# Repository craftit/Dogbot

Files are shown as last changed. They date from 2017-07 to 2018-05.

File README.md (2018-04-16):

# Dogbot

[DogBot] is a quadruped robot developed by [React AI] as a platform for researching robotics, AI and more.

The Dogbot repository contains CAD designs, along with software for higher-level systems for control and operation of the [React AI] DogBot robot via [ROS].  It utilises the lower-level motor control firmware in the corresponding [Firmware] repository for interaction with the physical DogBot.

# Installation

This code has been tested for installation and operation on Ubuntu Linux.

[ROS] must be installed; the code has been tested against the Kinetic release.  The repository contains a [catkin](http://wiki.ros.org/catkin) workspace under [Software/ROS](./Software/ROS), which should be built with `catkin build`

You may need to install the packages `ros-kinetic-rosparam-shortcuts ros-kinetic-ros-control ros-kinetic-ros-controllers` 

# Operation via Firmware and ROS

## Home the motors

The motors must be ‘homed’, i.e. know their absolute position, before they can be controlled via the ROS driver, hence they must first be controlled via the UI as described in the [Firmware] repo.

**Note:** complete the Firmware UI steps before starting the ROS components.  The hardware interface node in ROS will send conflicting signals if it is operational while the UI tries to alter the motor positions.

## Quick Start

To get started with ROS control, build and source the code then run `dogbot_hardware.launch`

```bat
cd Software/ROS
catkin build
source devel/setup.bash
roslaunch dogbot_control dogbot_hardware.launch
```

This launches a hardware interface node of type dogbot_control/dogbot_hw_main, which uses the [ros_control](http://wiki.ros.org/controller_manager) package to spawn and interact with ROS controllers.  This provides a framework for different controller types, as well as standardising interactions with Gazebo and RViz.

If you are controlling other equipment you may require a different launch file, such as testrig_hardware.launch

## Further ROS Control

The motors can now be controlled by interacting directly with ROS topics or via ROS nodes. Further details are in the ROS directory [readme file](./Software/ROS)

# Contributing

If you have any problems with the contents of either repository, or have a question about [DogBot], please feel free to [contact us](https://www.reactai.com/)

If you wish to contribute please fork the project on GitHub.  More details on contributing to follow.

# License

details to follow

[DogBot]: https://www.reactai.com/dog-bot/
[React AI]: https://www.reactai.com
[ROS]: http://www.ros.org
[Firmware]: https://github.com/craftit/BMC2-Firmware

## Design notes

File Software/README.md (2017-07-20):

Currently the motor controller firmware can be found in another repository.

  https://github.com/craftit/BMC2-Firmware

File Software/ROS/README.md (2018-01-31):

# Dogbot ROS Components

DogBot is integrated with ROS for ease of integration with your own systems.  Refer to the main [Dogbot repo] instructions for initial setup.

# Operation

## Initial Operation and Controllers

Interaction with the hardware requires the firmware components found in the [Firmware] repo, and the motors reqiure 'homing' via the firmware UI.  Once this is done, basic components can be run up using:

```bat
cd Software/ROS
catkin build
source devel/setup.bash
roslaunch dogbot_control dogbot_hardware.launch
```

12 controllers are instantiated, e.g. *front_right_knee_joint_controller*.  The [ros_control](http://wiki.ros.org/controller_manager) package is used to spawn and interact with ROS controllers, with the outline code beign built around Dave Coleman's [boilerplate] examples.

Currently the hardware interface only operates for position controllers, and only accepts absolute positions, not relative ones (hence the motors must be homed).

## Control via Topics, examples

Show the current joint states: ```rostopic echo -n 1 /dogbot/joint_states```

Sample output:
```
header: 
  seq: 307571
  stamp: 
    secs: 1517397784
    nsecs: 684705073
  frame_id: ''
name: [front_right_roll_joint, front_right_pitch_joint, front_right_knee_joint, front_left_roll_joint,
  front_left_pitch_joint, front_left_knee_joint, back_right_roll_joint, back_right_pitch_joint,
  back_right_knee_joint, back_left_roll_joint, back_left_pitch_joint, back_left_knee_joint]
position: [0.10201127827167511, 0.09683401137590408, 0.8471538424491882, 0.05003453932963618, -0.0013422536430880427, -0.010162778198719025, 0.00364325987175107, -0.002109255874529481, -0.012463783845305443, 0.006903018802404404, 0.013039035722613335, 0.0074782706797122955]
velocity: [0.0, 0.0, 0.0, 0.0, 0.0, 0.0, 0.0, 0.0, 0.0, 0.0, 0.0, 0.0]
acceleration: [0.0, 0.0, 0.0, 0.0, 0.0, 0.0, 0.0, 0.0, 0.0, 0.0, 0.0, 0.0]
```

Show just front_right_knee_joint position: ```rostopic echo -n 1 /dogbot/joint_states/position[2]```

Set a joint position:
```rostopic pub /dogbot/front_right_knee_position_controller/command std_msgs/Float64 "data: -1.0" -1```

[boilerplate]: https://github.com/davetcoleman/ros_control_boilerplate
[Dogbot repo]: https://github.com/craftit/Dogbot
[ROS]: http://www.ros.org
[Firmware]: https://github.com/craftit/BMC2-Firmware

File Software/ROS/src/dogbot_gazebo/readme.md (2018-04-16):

# dogbot_gazebo

Controls operation of simulated DogBot(s) in gazebo.  The robot description is in the dogbot_description package.

Control software is in dogbot_control, as the same software drives the simulation and the hardware

# Quick start

<pre>
cd Software/ROS
catkin build
source devel/setup.bash
roslaunch dogbot_gazebo gztest.launch
</pre>

Then to send commands to the joints and make the simulated DogBot move its legs around, in roughly a walking-on-the-spot motion, switch to another window and type:

<pre>
cd src/dogbot_gazebo/bags/
rosbag play -l demo1.bag
</pre>

# Launch files

Top-level files start with gz

Other files are components, intended to be included into the higher-level files (esp. to set the namespace correctly)

# Prerequisites

Ensure you have gazebo-ros control packages installed, http://wiki.ros.org/gazebo_ros_control

<pre>sudo apt-get install ros-kinetic-gazebo-ros-pkgs ros-kinetic-gazebo-ros-control</pre>

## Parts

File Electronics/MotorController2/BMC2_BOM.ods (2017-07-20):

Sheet: BMC2
Reference | Value | Footprint | Datasheet | Done
U1 | TJA1042T/3 | Housings_SOIC:SOIC-8_3.9x4.9mm_Pitch1.27mm |  | x
P2 | CAN
C1 | 0.1uf (6V min) | Capacitors_SMD:C_0805_HandSoldering |  | x
P4 | USB_OTG
R9 | 22R | Resistors_SMD:R_0805_HandSoldering |  | x
R10 | 22R | Resistors_SMD:R_0805_HandSoldering |  | x
D1 | 10V | Diodes_SMD:DO-214AB_Handsoldering |  | x
R1 | 1k | Resistors_SMD:R_0805_HandSoldering |  | x
R2 | 1k | Resistors_SMD:R_0805_HandSoldering |  | x
R3 | 1k | Resistors_SMD:R_0805_HandSoldering |  | x
R4 | 1k | Resistors_SMD:R_0805_HandSoldering |  | x
R5 | 1k | Resistors_SMD:R_0805_HandSoldering |  | x
R8 | 1k | Resistors_SMD:R_0805_HandSoldering |  | x
R7 | 10k | Resistors_SMD:R_0805_HandSoldering |  | x
C2 | 0.1uF | Capacitors_SMD:C_0805_HandSoldering |  | x
R6 | 1k | Resistors_SMD:R_0805_HandSoldering |  | x
P3 | DATA
P5 | PhaseA
P6 | PhaseB
P7 | PhaseC
W1 | TEST_1P
W2 | TEST_1P
P1 | Sensor
P9 | VSUPPLY
P10 | GND
X1 | 8MHz
C5 | 15pF | Capacitors_SMD:C_0805_HandSoldering |  | x
C6 | 15pF | Capacitors_SMD:C_0805_HandSoldering |  | x
P8 | CONN_02X05
C13 | 100nf | Capacitors_SMD:C_0805_HandSoldering |  | x
C10 | 100nf | Capacitors_SMD:C_0805_HandSoldering |  | x
C12 | 100nf | Capacitors_SMD:C_0805_HandSoldering |  | x
C11 | 100nf | Capacitors_SMD:C_0805_HandSoldering |  | x
C9 | 100nf 5V | Capacitors_SMD:C_0805_HandSoldering |  | x
C8 | 4.7uf | Capacitors_SMD:C_1206_HandSoldering |  | x
C14 | 1uf | Capacitors_SMD:C_0805_HandSoldering |  | x
R13 | 10R | Resistors_SMD:R_0805_HandSoldering |  | x
L1 | INDUCTOR | Resistors_SMD:R_0805_HandSoldering
C7 | 100nf | Capacitors_SMD:C_0805_HandSoldering |  | x
SW1 | RESET
JP2 | Jumper_NC_Small | Resistors_SMD:R_0805_HandSoldering |  | x
JP1 | Jumper_NO_Small | Resistors_SMD:R_0805_HandSoldering |  | x
C4 | 2.2uf | Capacitors_SMD:C_0805_HandSoldering |  | x
C3 | 2.2uf | Capacitors_SMD:C_0805_HandSoldering |  | x
U2 | STM32F205RBTx | LQFP64
R11 | 100R | Resistors_SMD:R_0805_HandSoldering |  | x
D2 | GREEN LED | LEDs:LED_0805
R12 | 100R | Resistors_SMD:R_0805_HandSoldering |  | x
D3 | RED LED | LEDs:LED_0805
R16 | 10K | Resistors_SMD:R_0805_HandSoldering |  | x
R17 | 10K | Resistors_SMD:R_0805_HandSoldering |  | x
C16 | 0.1uF 5V | Capacitors_SMD:C_0805_HandSoldering |  | x
R15 | 10K | Resistors_SMD:R_0805_HandSoldering |  | x
SW2 | CAL
R14 | 10K | Resistors_SMD:R_0805_HandSoldering |  | x
C15 | 0.1uF 5V | Capacitors_SMD:C_0805_HandSoldering |  | x
W14 | TEST_1P
U3 | DRV8305 |  |  | x
R19 | 10K | Resistors_SMD:R_0805_HandSoldering |  | x
R18 | 10K | Resistors_SMD:R_0805_HandSoldering |  | x
C23 | 0.047uf 45v | Capacitors_SMD:C_1206_HandSoldering |  | x
C22 | 0.047uf 90V | Capacitors_SMD:C_1206_HandSoldering |  | x
C20 | 1uf 6.3V | Capacitors_SMD:C_0805_HandSoldering |  | x
C19 | 1uf 6.3V | Capacitors_SMD:C_0805_HandSoldering |  | x
C18 | 1uf 16V | Capacitors_SMD:C_1206_HandSoldering |  | x
C27 | 2.2uf 16V | Capacitors_SMD:C_1206_HandSoldering |  | x
C28 | 4.7uF 45V | Capacitors_SMD:C_1206_HandSoldering |  | x
R22 | 100R | Resistors_SMD:R_0805_HandSoldering |  | x
R26 | R001
R25 | R001
R24 | R001
Q3 | BSC016N06NS
Q4 | BSC016N06NS
Q6 | BSC016N06NS
Q5 | BSC016N06NS
Q1 | BSC016N06NS
Q2 | BSC016N06NS
R29 | 39K | Resistors_SMD:R_0805_HandSoldering |  | x
R30 | 3K | Resistors_SMD:R_0805_HandSoldering |  | x
R31 | 39K | Resistors_SMD:R_0805_HandSoldering |  | x
R32 | 3K | Resistors_SMD:R_0805_HandSoldering |  | x
C35 | 30pF 5V | Capacitors_SMD:C_0805_HandSoldering |  | x
C34 | 30pF 5V | Capacitors_SMD:C_0805_HandSoldering |  | x
R27 | 39K | Resistors_SMD:R_0805_HandSoldering |  | x
R28 | 3K | Resistors_SMD:R_0805_HandSoldering |  | x
C33 | 30pF 5V | Capacitors_SMD:C_0805_HandSoldering |  | x
C30 | 0.1uf 50V min | Capacitors_SMD:C_1206_HandSoldering |  | x
C31 | 0.1uf (Min 50V) | Capacitors_SMD:C_1206_HandSoldering |  | x
C32 | 0.1uf (Min 50V) | Capacitors_SMD:C_1206_HandSoldering |  | x
R20 | 39K | Resistors_SMD:R_0805_HandSoldering |  | x
R21 | 3K | Resistors_SMD:R_0805_HandSoldering |  | x
C21 | 0.1uF 5V | Capacitors_SMD:C_0805_HandSoldering |  | x
C17 | 1uF 4V | Capacitors_SMD:C_0805_HandSoldering |  | x
C24 | 1nF 5V | Capacitors_SMD:C_0805_HandSoldering |  | x
C26 | 1nF 5V | Capacitors_SMD:C_0805_HandSoldering |  | x
C29 | 1nf 5V | Capacitors_SMD:C_0805_HandSoldering |  | x
W5 | TEST_1P
W4 | TEST_1P
W3 | TEST_1P
W7 | GHA
W8 | GLA
W9 | SLA
W6 | SHA
C25 | 0.1uF 5V | Capacitors_SMD:C_0805_HandSoldering |  | x
R23 | 10K | Resistors_SMD:R_0805_HandSoldering |  | x
TH1 | THERMISTOR
C38 | 22nF 6V | Capacitors_SMD:C_0805_HandSoldering |  | x
R33 | 22k | Resistors_SMD:R_0805_HandSoldering |  | x
D4 | D | Diodes_SMD:DO-214AB_Handsoldering |  | x
C36 | 220nF 60V | Capacitors_SMD:C_1206_HandSoldering |  | x
L2 | 47uH | Inductors:SELF-WE-PD3S
C39 | 220nF 60V | Capacitors_SMD:C_1206_HandSoldering |  | x
C37 | 100uF 60V | Capacitors_SMD:c_elec_10x10.5 |  | x
C40 | 220nF 6V | Capacitors_SMD:C_0805_HandSoldering |  | x
D6 | 50V | Diodes_SMD:SOD-123 |  | x
C41 | 100uF 6V | Capacitors_SMD:c_elec_6.3x5.8 |  | x
C42 | 220nF 6V | Capacitors_SMD:C_0805_HandSoldering |  | x
L3 | 47uH | Inductors:SELF-WE-PD3S
D7 | 5.6V | Diodes_SMD:SOD-123 |  | x
D9 | LED | LEDs:LED_0805
R34 | 100R | Resistors_SMD:R_0805_HandSoldering |  | x
U4 | IFX91041EJV50
D5 | D | Diodes_SMD:DO-214AB_Handsoldering |  | x
C43 | 1uF 4V min | Capacitors_SMD:C_0805_HandSoldering |  | x
D8 | 3.6V | Diodes_SMD:SOD-123 |  | x
U5 | TC2117-3.3V |  |  | x
W12 | 5V
W13 | 3V3
W10 | DSUP
W11 | GND

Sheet: Sheet2
Boards | 12
Part | Footprint | Per Board | Total | Farnell code
1K | R 0805 | 7 | 84 | 2447587
10K | R 0805 | 8 | 96 | 9332391
22R | R 0805 | 2 | 24 | 2447609
100R | R 0805 | 4 | 48 | 9333703
39K | R 0805 | 4 | 48 | 2447646
3K | R 0805 | 4 | 48 | 2447648
22K | R 0805 | 1 | 12 | 2447607
0.1uF 50V | C 0805 | 13 | 156 | 1759265
0.1uF 250V | C 1206 | 3 | 36 | 1828957
15pf | C 0805 | 2 | 24 | 2497014
4.7uF 25V | C 1206 | 1 | 12 | 1828835
4.7uF 100V | C 1206 | 1 | 12 | 2310265
1uf 50V | C 0805 | 6 | 72 | 1759432
1uF 100V | C 1206 | 4 | 48 | 2320876
2.2uF 50V | C 0805 | 2 | 24 | 2611933
2.2uF 50V | C 1206 | 1 | 12 | 1797017
30pf | C 0805 | 3 | 36 | 2581093
47nf 200V | C 1206 | 2 | 24 | 1855874
0R | R 0805 | 2 | 24 | 2309111
1nF 50V | C 0805 | 6 | 72 | 9406344
22nF | C 0805 | 1 | 12 | 2320841
220nf 100V | C 1206 | 2 | 24 | 1856615
100uf 63V | c_elec_10x10.5 | 1 | 12 | 9696040
220nf | C 0805 | 2 | 24 | 1759173
100uf | c_elec_6.3x5.8 | 1 | 12 | 2611349
Schottky 60V | SOD-123 | 4 | 48 | 2284958
TC2117-3.3V |  | 1 | 12 | 1605581
Zener 3.6V | SOD-123 | 1 | 12 | 1651592
Zener 5.6V | SOD-123 | 1 | 12 | 1431292
Thermistor | R 0805 | 2 | 24 | 2103179
LED Green | LED 0805 | 1 | 12 | 1465996
LED Red | LED 0805 | 1 | 12 | 1581239
LED Yellow | LED 0805 | 1 | 12 | 1581241
10uH | L 0805 | 1 | 12 | 2215650
9 Way Right Angle |  | 1 | 12 | 2468365
4 way Right Angle |  | 2 | 24 | 588738
5 way right angle |  | 1 | 12 | 588740
push button |  | 2 | 24 | 2468741
10R | R 0805 | 1 | 12 | 2447556

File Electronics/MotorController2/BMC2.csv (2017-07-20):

Reference, Quantity, Value, Footprint, Datasheet, Order, Farnell, Farnell Related, Plug Farnell, Notes, Note, Order2, Part, Type
C1 C10 C11 C12 C13 C15 C16 C2 C21 C25 C44 C7 C9 ,13,"0.1uF 50V","Capacitors_SMD:C_0805_HandSoldering","","","","","","",",","1759265",",",",",",","
C14 C17 C19 C20 C43 ,5,"1uF 50V","Capacitors_SMD:C_0805_HandSoldering","","","","","","",",","1759432",",","5V",",",","
C18 C30 C31 C32 ,4,"1uF 100V","Capacitors_SMD:C_1206_HandSoldering","","","","","","",",","2320876",",","16V",",",","
C22 C23 ,2,"47nF 200V","Capacitors_SMD:C_1206_HandSoldering","","","","","","",",","1855874",",","45V",",",","
C27 ,1,"2.2uF 50V","Capacitors_SMD:C_1206_HandSoldering","","","","","","",",","1797017",",","16V",",",","
C28 ,1,"4.7uF 100V","Capacitors_SMD:C_1206_HandSoldering","","","","","","",",","1797017",",","45V",",",","
C33 C34 C35 ,3,"30pF 5V","Capacitors_SMD:C_0805_HandSoldering","","","","","","",",","2581093",",",",",",","
C36 C39 ,2,"220nF 100V","Capacitors_SMD:C_1206_HandSoldering","","","","","","",",","1856615",",",",",",","
C37 ,1,"100uF 63V","Capacitors_SMD:c_elec_10x10.5","","","","","","",",","9696040",",",",",",","
C38 ,1,"22nF 50V","Capacitors_SMD:C_0805_HandSoldering","","","","","","",",","2581093",",","6V",",",","
C3 C4 ,2,"2.2uF 50V","Capacitors_SMD:C_0805_HandSoldering","","","","","","",",","2611933",",",",",",","
C40 C42 ,2,"220nF 100V","Capacitors_SMD:C_0805_HandSoldering","","","","","","",",","1856615",",","6V",",",","
C41 ,1,"100uF 6.3V","Capacitors_SMD:c_elec_6.3x5.8","","","","","","",",","2611349",",",",",",","
C24 C26 C29 C45 C46 C47 ,6,"1nF 50V","Capacitors_SMD:C_0805_HandSoldering","","","","","","",",","9406344",",",",",",","
C5 C6 ,2,"15pF","Capacitors_SMD:C_0805_HandSoldering","","","","","","",",","2497014",",",",",",","
C8 ,1,"4.7uF 25V","Capacitors_SMD:C_1206_HandSoldering","","","","","","",",","1828835",",",",",",","
D1 D4 D5 D6 ,4,"60V 2A","Diodes_SMD:SOD-123","","","","","","",",","2284958",",",",",",","
D2 ,1,"GREEN LED","LEDs:LED_0805","","","","","","",",","1465996",",","2V",",",","
D3 ,1,"YELLOW","LEDs:LED_0805","","","","","","",",","1581241",",",",",",","
D7 ,1,"5.6V","Diodes_SMD:SOD-123","","","","","","",","http://uk.farnell.com/on-semiconductor/mmsz5v6t1g/diode-zener-5-6v-0-5w/dp/1431292","1431292",",",",",","MMSZ5V6T1G","
D8 ,1,"3.6V","Diodes_SMD:SOD-123","","","","","","",","http://uk.farnell.com/on-semiconductor/mmsz4685t1g/diode-zener-vz-3-6v/dp/1651592","1651592",",",",",","MMSZ4685T1G","
D9 ,1,"RED","LEDs:LED_0805","","","","","","",",","1581239",",",",",",","
JP1 ,1,"Jumper_NO_Small","Resistors_SMD:R_0805_HandSoldering","","","","","","","
JP2 ,1,"Jumper_NC_Small","Resistors_SMD:R_0805_HandSoldering","","","","","","","
L1 ,1,"10uH","Resistors_SMD:R_0805_HandSoldering","","","","","","",",","2215650",",",",",",","
L2 L3 ,2,"47uH","Inductors:SELF-WE-PD3S","","","","","","",","http://uk.farnell.com/tdk/clf7045t-470m/inductor-47uh-1-3a-20-smd/dp/2345091",",",",",",",","
P1 ,1,"Sensor","Pin_Headers:Pin_Header_Angled_1x09","","","","","","",",","2468365",","1098695",",",",","
P10 ,1,"GND","Connect:1pin","","","","","","","
P11 ,1,"I2C","Pin_Headers:Pin_Header_Straight_1x04","","","","","","",","http://uk.farnell.com/molex/171856-0004/connector-header-tht-2-54mm-4way/dp/2366182",",",",",",",","
P12 P2 ,2,"CAN","Pin_Headers:Pin_Header_Angled_1x04","","","","","","",",","588738","1098455",",",",",","
P3 ,1,"DATA","Pin_Headers:Pin_Header_Angled_1x05","","","","","","",",","588740",",",",",",","
P4 ,1,"USB_OTG","Connect:USB_Mini-B","","","","","","",","http://uk.farnell.com/molex/67503-1020/mini-usb-2-0-otg-type-b-rcpt-smt/dp/1125348",",",",",",",","
P5 ,1,"PhaseA","Connect:1pin","","","","","","","
P6 ,1,"PhaseB","Connect:1pin","","","","","","","
P7 ,1,"PhaseC","Connect:1pin","","","","","","","
P8 ,1,"CONN_02X05","Local:SMT-HDR-10","","","","","","",","http://uk.rs-online.com/web/p/pcb-headers/0451732/?searchTerm=FTSH-105-01-F-DV-K&autocorrected=y",",",",",",",","
P9 ,1,"VSUPPLY","Connect:1pin","","","","","","","
Q1 Q2 Q3 Q4 Q5 Q6 ,6,"BSC016N06NS","Local:SON127P532X615X110-8N","","","","","","","
R1 R2 R3 R4 R5 R6 R8 ,7,"1k","Resistors_SMD:R_0805_HandSoldering","","","","","","",","http://uk.farnell.com/multicomp/mcwr08x1001ftl/res-thick-film-1k-1-0-125w-0805/dp/2447587",",",",",",",","
R11 R12 R22 R34 ,4,"100R","Resistors_SMD:R_0805_HandSoldering","","","","","","","
R13 ,1,"10","Resistors_SMD:R_0805_HandSoldering","","","","","","","
R24 R25 R26 ,3,"R001","Local:R_PSR400_SENSE","","","","","","","
R20 R27 R29 R31 ,4,"39K","Resistors_SMD:R_0805_HandSoldering","","","","","","","
R21 R28 R30 R32 ,4,"3K","Resistors_SMD:R_0805_HandSoldering","","","","","","","
R33 ,1,"22k","Resistors_SMD:R_0805_HandSoldering","","","","","","","
R14 R15 R16 R17 R18 R19 R23 R7 ,8,"10K","Resistors_SMD:R_0805_HandSoldering","","","","","","","
R10 R9 ,2,"22R","Resistors_SMD:R_0805_HandSoldering","","","","","","","
SW1 ,1,"RESET","Buttons_Switches_SMD:SW_SPST_FSMSM","","","","","","",",","42468741",",",",",",","
SW2 ,1,"CAL","Buttons_Switches_SMD:SW_SPST_FSMSM","","","","","","",","http://uk.farnell.com/alcoswitch-te-connectivity/1437566-3/pushbutton-switch-spst-0-05a-24v/dp/2468741","2468741",",",",",",","
TH1 ,1,"NTC 10K","Resistors_SMD:R_0805_HandSoldering","","","","","","",","http://uk.farnell.com/vishay/ntcs0805e3103jlt/thermistor-10k-5-smd-ntc/dp/2103179","2103179",",",",",",","
U1 ,1,"TJA1042T/3","Housings_SOIC:SOIC-8_3.9x4.9mm_Pitch1.27mm","","","","","","",","http://uk.farnell.com/nxp/tja1042t-3-1j/can-transceiver-aec-q100-2mbps/dp/2574957",",",",",",",","
U2 ,1,"STM32F205RBTx","Housings_QFP:LQFP-64_10x10mm_Pitch0.5mm","","","","","","","
U3 ,1,"DRV8305","QFP50P900X900X120-49N:QFP50P900X900X120-49N","","","","","","","
U4 ,1,"IFX91041EJV50","Housings_SOIC:SOIC-8-1EP_3.9x4.9mm_Pitch1.27mm","","","","","","",","https://www.digikey.co.uk/product-detail/en/infineon-technologies/IFX91041EJ-V50/IFX91041EJ-V50INCT-ND/3300395",",",",",",",","
U5 ,1,"TC2117-3.3V","TO_SOT_Packages_SMD:SOT-223","","","","","","",","http://uk.farnell.com/microchip/tc2117-3-3vdbtr/ic-cmso-ldo-3-3v-800ma-sot223/dp/1605581",",",",",",",","
W1 ,1,"CAN_TX","Measurement_Points:Measurement_Point_Round-SMD-Pad_Small","","","","","","","
W10 ,1,"DSUP","Measurement_Points:Measurement_Point_Round-SMD-Pad_Small","","","","","","","
W11 ,1,"GND","Measurement_Points:Measurement_Point_Round-SMD-Pad_Big","","","","","","","
W12 ,1,"5V","Measurement_Points:Measurement_Point_Round-SMD-Pad_Small","","","","","","","
W13 ,1,"3V3","Measurement_Points:Measurement_Point_Round-SMD-Pad_Small","","","","","","","
W14 ,1,"PB12","Measurement_Points:Measurement_Point_Round-SMD-Pad_Small","","","","","","","
W2 ,1,"CAN_RX","Measurement_Points:Measurement_Point_Round-SMD-Pad_Small","","","","","","","
W3 ,1,"ISenseA","Measurement_Points:Measurement_Point_Round-SMD-Pad_Small","","","","","","","
W4 ,1,"ISenseB","Measurement_Points:Measurement_Point_Round-SMD-Pad_Small","","","","","","","
W5 ,1,"ISenseC","Measurement_Points:Measurement_Point_Round-SMD-Pad_Small","","","","","","","
W7 ,1,"GHA","Measurement_Points:Measurement_Point_Round-SMD-Pad_Small","","","","","","","
W8 ,1,"GLA","Measurement_Points:Measurement_Point_Round-SMD-Pad_Small","","","","","","","
X1 ,1,"8MHz","Crystals:ABM3","","","","","","",","http://uk.farnell.com/abracon/abm3-8-000mhz-d2y-t/crystal-8mhz-18pf-smd/dp/2101329",",",",",",",","

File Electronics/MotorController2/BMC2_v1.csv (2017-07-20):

Reference | Value | Footprint | Datasheet
U1 | TJA1042T/3 | Housings_SOIC:SOIC-8_3.9x4.9mm_Pitch1.27mm
P2 | CAN
C1 | 0.1uf (6V min) | Capacitors_SMD:C_0805_HandSoldering
P4 | USB_OTG
R9 | 22R | Resistors_SMD:R_0805_HandSoldering
R10 | 22R | Resistors_SMD:R_0805_HandSoldering
D1 | 10V | Diodes_SMD:DO-214AB_Handsoldering
R1 | 1k | Resistors_SMD:R_0805_HandSoldering
R2 | 1k | Resistors_SMD:R_0805_HandSoldering
R3 | 1k | Resistors_SMD:R_0805_HandSoldering
R4 | 1k | Resistors_SMD:R_0805_HandSoldering
R5 | 1k | Resistors_SMD:R_0805_HandSoldering
R8 | 1k | Resistors_SMD:R_0805_HandSoldering
R7 | 10k | Resistors_SMD:R_0805_HandSoldering
C2 | 0.1uF | Capacitors_SMD:C_0805_HandSoldering
R6 | 1k | Resistors_SMD:R_0805_HandSoldering
P3 | DATA
P5 | PhaseA
P6 | PhaseB
P7 | PhaseC
W1 | TEST_1P
W2 | TEST_1P
P1 | Sensor
P9 | VSUPPLY
P10 | GND
X1 | 8MHz
C5 | 15pF | Capacitors_SMD:C_0805_HandSoldering
C6 | 15pF | Capacitors_SMD:C_0805_HandSoldering
P8 | CONN_02X05
C13 | 10nf | Capacitors_SMD:C_0805_HandSoldering
C10 | 100nf | Capacitors_SMD:C_0805_HandSoldering
C12 | 100nf | Capacitors_SMD:C_0805_HandSoldering
C11 | 100nf | Capacitors_SMD:C_0805_HandSoldering
C9 | 100nf 5V | Capacitors_SMD:C_0805_HandSoldering
C8 | 4.7uf | Capacitors_SMD:C_1206_HandSoldering
C14 | 1uf | Capacitors_SMD:C_0805_HandSoldering
R13 | 10 | Resistors_SMD:R_0805_HandSoldering
L1 | INDUCTOR | Resistors_SMD:R_0805_HandSoldering
C7 | 100nf | Capacitors_SMD:C_0805_HandSoldering
SW1 | RESET
JP2 | Jumper_NC_Small | Resistors_SMD:R_0805_HandSoldering
JP1 | Jumper_NO_Small | Resistors_SMD:R_0805_HandSoldering
C4 | 2.2uf | Capacitors_SMD:C_0805_HandSoldering
C3 | 2.2uf | Capacitors_SMD:C_0805_HandSoldering
U2 | STM32F205RBTx | LQFP64
R11 | 100R | Resistors_SMD:R_0805_HandSoldering
D2 | GREEN LED | LEDs:LED_0805
R12 | 100R | Resistors_SMD:R_0805_HandSoldering
D3 | RED LED | LEDs:LED_0805
R16 | 10K | Resistors_SMD:R_0805_HandSoldering
R17 | 10K | Resistors_SMD:R_0805_HandSoldering
C16 | 0.1uF 5V | Capacitors_SMD:C_0805_HandSoldering
R15 | 10K | Resistors_SMD:R_0805_HandSoldering
SW2 | CAL
R14 | 10K | Resistors_SMD:R_0805_HandSoldering
C15 | 0.1uF 5V | Capacitors_SMD:C_0805_HandSoldering
W14 | TEST_1P
U3 | DRV8305
R19 | 10K | Resistors_SMD:R_0805_HandSoldering
R18 | 10K | Resistors_SMD:R_0805_HandSoldering
C23 | 0.047uf 45v | Capacitors_SMD:C_1206_HandSoldering
C22 | 0.047uf 90V | Capacitors_SMD:C_1206_HandSoldering
C20 | 1uf 6.3V | Capacitors_SMD:C_0805_HandSoldering
C19 | 1uf 6.3V | Capacitors_SMD:C_0805_HandSoldering
C18 | 1uf 16V | Capacitors_SMD:C_1206_HandSoldering
C27 | 2.2uf 16V | Capacitors_SMD:C_1206_HandSoldering
C28 | 4.7uF 45V | Capacitors_SMD:C_1206_HandSoldering
R22 | 100R | Resistors_SMD:R_0805_HandSoldering
R26 | R001
R25 | R001
R24 | R001
Q3 | BSC016N06NS
Q4 | BSC016N06NS
Q6 | BSC016N06NS
Q5 | BSC016N06NS
Q1 | BSC016N06NS
Q2 | BSC016N06NS
R29 | 39K | Resistors_SMD:R_0805_HandSoldering
R30 | 3K | Resistors_SMD:R_0805_HandSoldering
R31 | 39K | Resistors_SMD:R_0805_HandSoldering
R32 | 3K | Resistors_SMD:R_0805_HandSoldering
C35 | 30pF 5V | Capacitors_SMD:C_0805_HandSoldering
C34 | 30pF 5V | Capacitors_SMD:C_0805_HandSoldering
R27 | 39K | Resistors_SMD:R_0805_HandSoldering
R28 | 3K | Resistors_SMD:R_0805_HandSoldering
C33 | 30pF 5V | Capacitors_SMD:C_0805_HandSoldering
C30 | 0.1uf 50V min | Capacitors_SMD:C_1206_HandSoldering
C31 | 0.1uf (Min 50V) | Capacitors_SMD:C_1206_HandSoldering
C32 | 0.1uf (Min 50V) | Capacitors_SMD:C_1206_HandSoldering
R20 | 39K | Resistors_SMD:R_0805_HandSoldering
R21 | 3K | Resistors_SMD:R_0805_HandSoldering
C21 | 0.1uF 5V | Capacitors_SMD:C_0805_HandSoldering
C17 | 1uF 4V | Capacitors_SMD:C_0805_HandSoldering
C24 | 1nF 5V | Capacitors_SMD:C_0805_HandSoldering
C26 | 1nF 5V | Capacitors_SMD:C_0805_HandSoldering
C29 | 1nf 5V | Capacitors_SMD:C_0805_HandSoldering
W5 | TEST_1P
W4 | TEST_1P
W3 | TEST_1P
W7 | GHA
W8 | GLA
W9 | SLA
W6 | SHA
C25 | 0.1uF 5V | Capacitors_SMD:C_0805_HandSoldering
R23 | 10K | Resistors_SMD:R_0805_HandSoldering
TH1 | THERMISTOR
C38 | 22nF 6V | Capacitors_SMD:C_0805_HandSoldering
R33 | 22k | Resistors_SMD:R_0805_HandSoldering
D4 | D | Diodes_SMD:DO-214AB_Handsoldering
C36 | 220nF 60V | Capacitors_SMD:C_1206_HandSoldering
L2 | 47uH | Inductors:SELF-WE-PD3S
C39 | 220nF 60V | Capacitors_SMD:C_1206_HandSoldering
C37 | 100uF 60V | Capacitors_SMD:c_elec_10x10.5
C40 | 220nF 6V | Capacitors_SMD:C_0805_HandSoldering
D6 | 50V | Diodes_SMD:SOD-123
C41 | 100uF 6V | Capacitors_SMD:c_elec_6.3x5.8
C42 | 220nF 6V | Capacitors_SMD:C_0805_HandSoldering
L3 | 47uH | Inductors:SELF-WE-PD3S
D7 | 5.4V | Diodes_SMD:SOD-123
D9 | LED | LEDs:LED_0805
R34 | 100R | Resistors_SMD:R_0805_HandSoldering
U4 | IFX91041EJV50
D5 | D | Diodes_SMD:DO-214AB_Handsoldering
C43 | 1uF 4V min | Capacitors_SMD:C_0805_HandSoldering
D8 | 3.6V | Diodes_SMD:SOD-123
U5 | TC2117-3.3V
W12 | 5V
W13 | 3V3
W10 | DSUP
W11 | GND

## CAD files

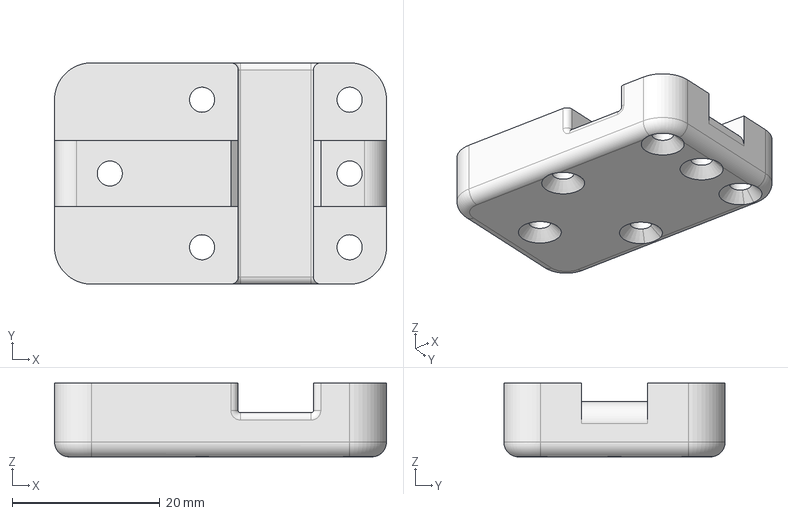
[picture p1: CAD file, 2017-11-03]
CAD/Body/BatteryMountV3.FCStd
45.0 x 30.0 x 10.0 mm

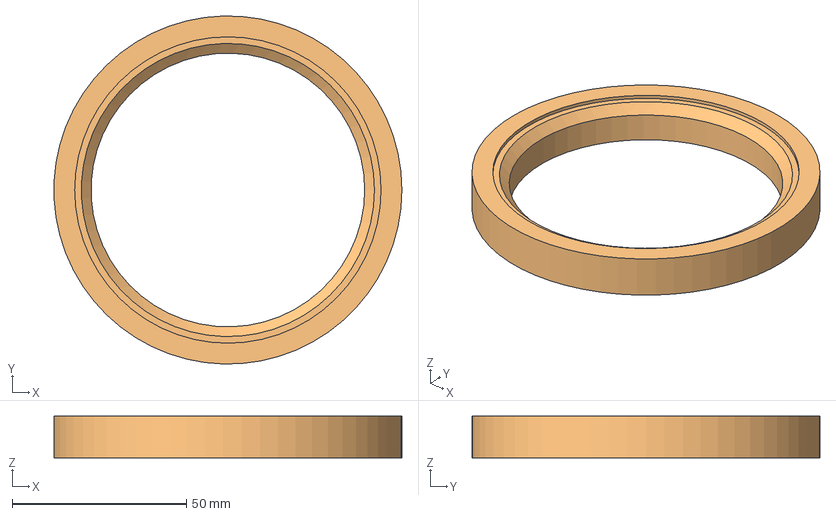
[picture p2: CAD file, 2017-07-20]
CAD/Experiments/TestOuterRace.FCStd
99.9 x 100.0 x 12.0 mm
PolarPattern

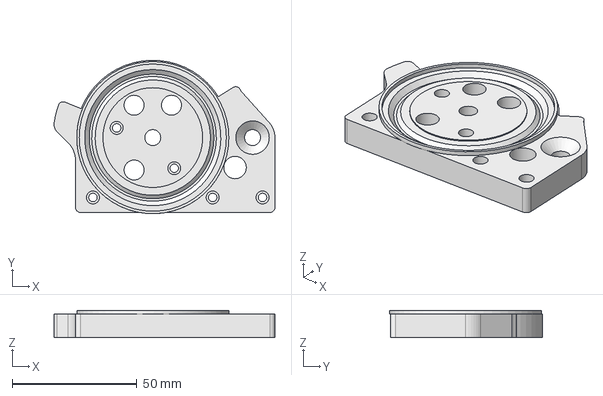
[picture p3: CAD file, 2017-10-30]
CAD/Leg/LowerKneeRaceV4.FCStd
88.6 x 61.5 x 11.0 mm

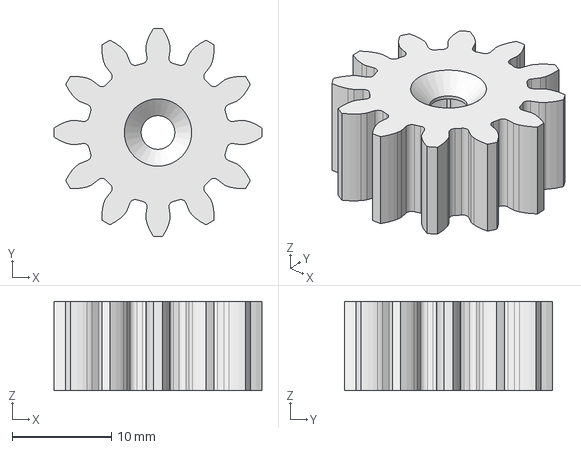
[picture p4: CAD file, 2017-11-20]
CAD/Servo/SunGearV2_145mod.FCStd
21.0 x 21.0 x 9.00 mm

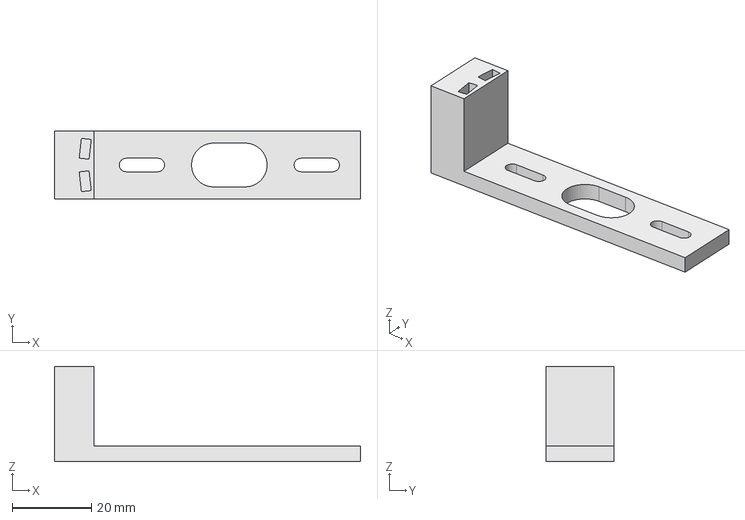
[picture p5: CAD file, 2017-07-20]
CAD/Experiments/MotorSensorTest.FCStd
77.0 x 17.0 x 24.0 mm

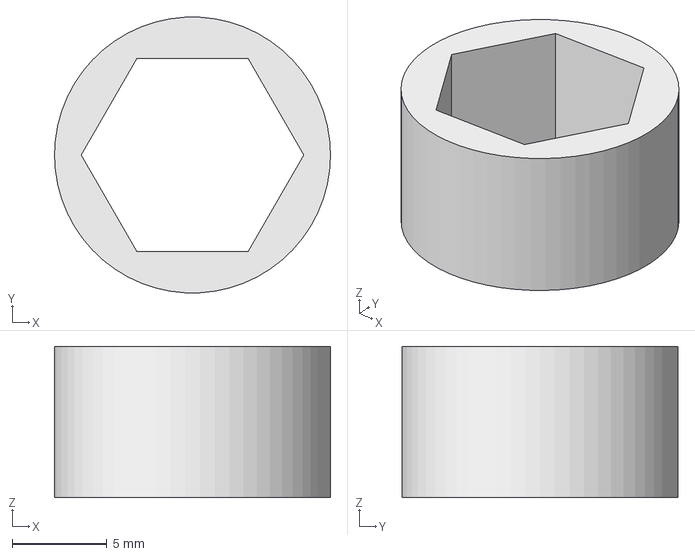
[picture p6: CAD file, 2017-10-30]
CAD/Leg/DriveLinkV2B-15mm.FCStd
14.6 x 14.6 x 8.00 mm

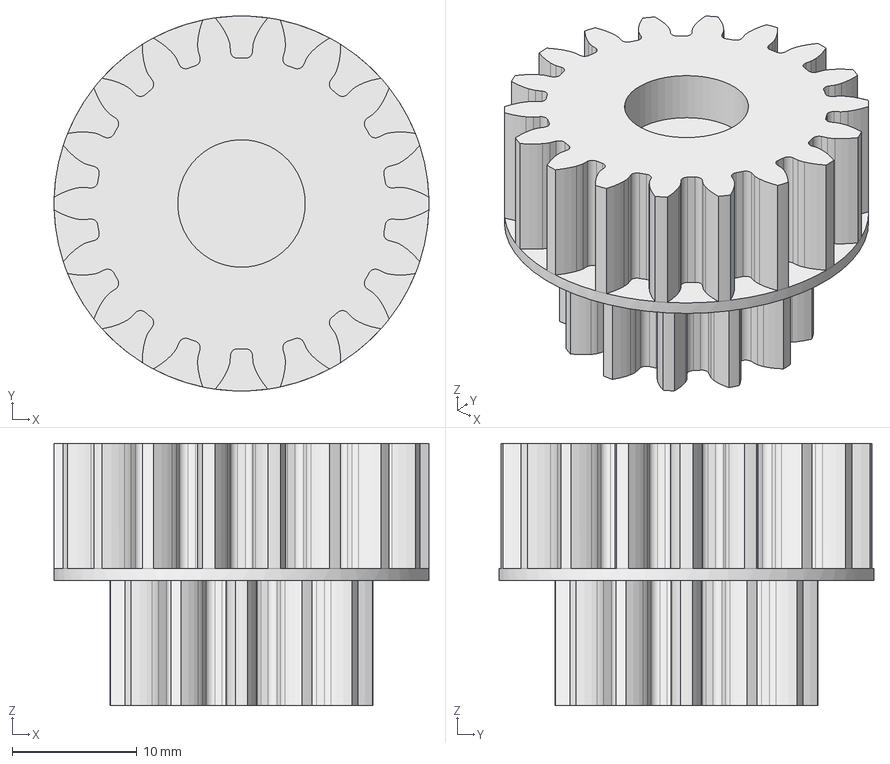
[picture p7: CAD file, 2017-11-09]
CAD/Servo/PlanetGear12_18l_Large_V3.FCStd
30.0 x 30.0 x 21.0 mm

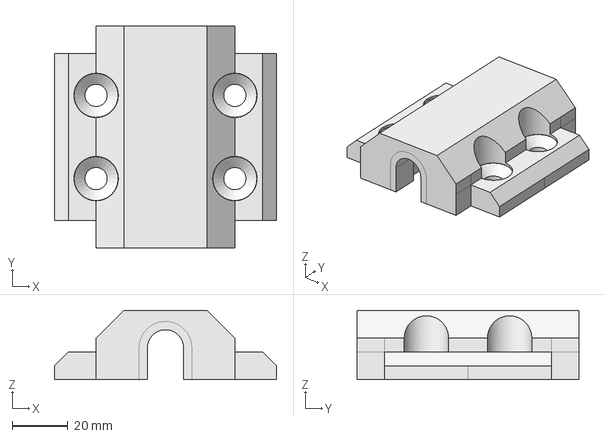
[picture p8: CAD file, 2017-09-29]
CAD/TestRigs/TestRig_bearing-housing.fcstd
80.0 x 80.0 x 25.0 mm

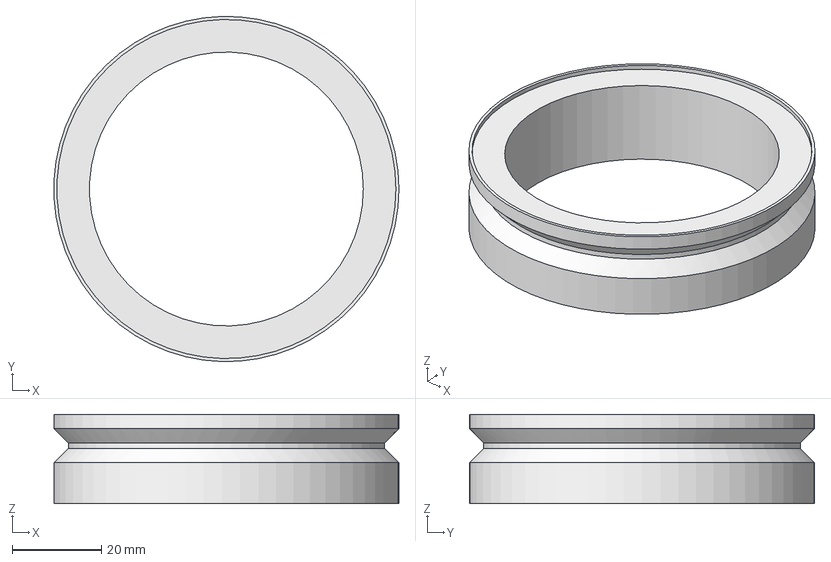
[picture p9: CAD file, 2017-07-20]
CAD/Experiments/TestRace.FCStd
77.3 x 77.4 x 20.0 mm

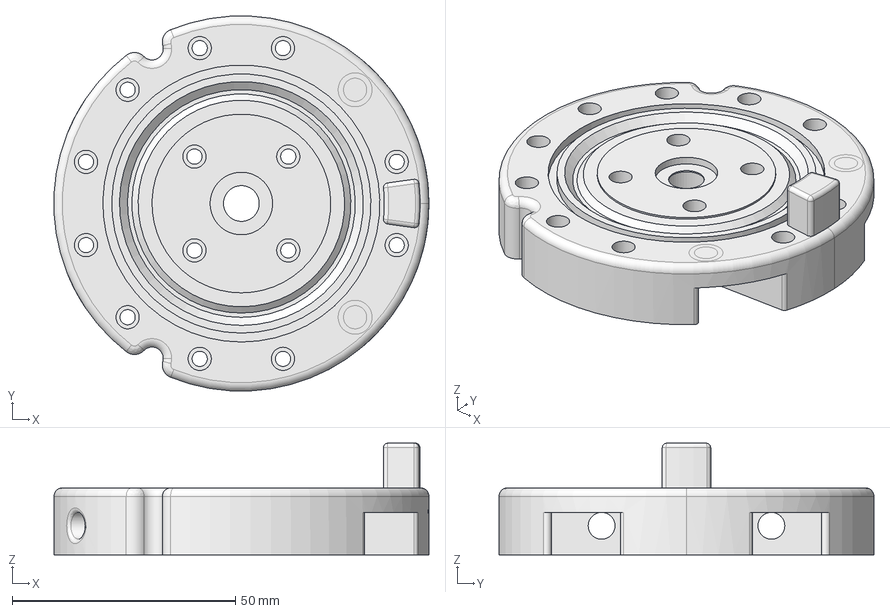
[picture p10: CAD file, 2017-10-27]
CAD/Leg/UpperKnee4-15_5mm.FCStd
83.9 x 83.9 x 25.0 mm

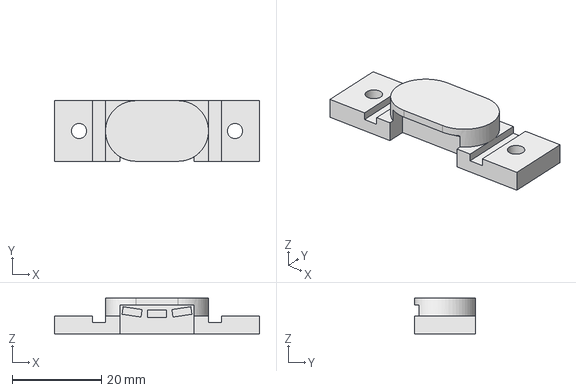
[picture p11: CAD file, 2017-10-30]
CAD/Servo/MotorHall3SensorMountPCB.FCStd
46.0 x 13.6 x 8.00 mm

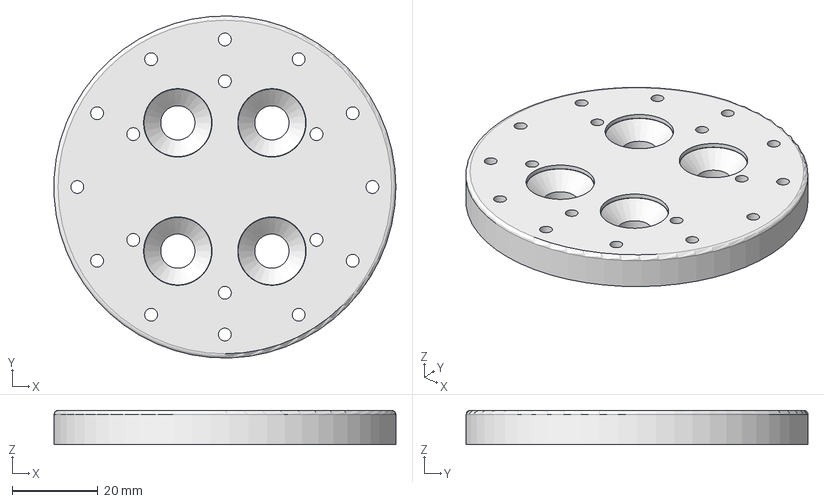
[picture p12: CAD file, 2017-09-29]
CAD/TestRigs/TestRig_DummyRingDrive3.fcstd
79.9 x 80.0 x 8.00 mm

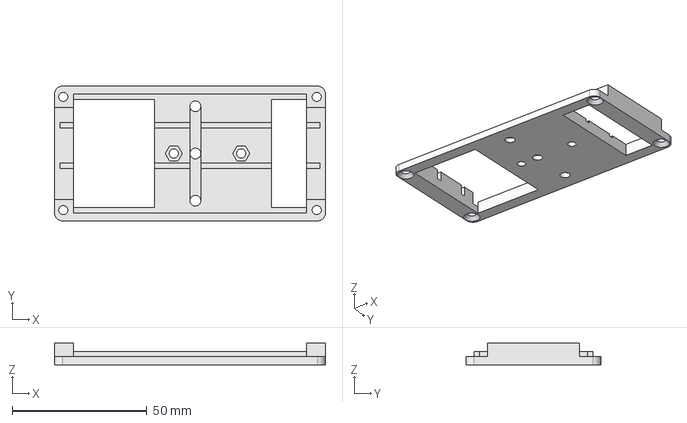
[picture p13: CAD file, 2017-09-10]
CAD/Body/MotorDriverMountB.FCStd
100.5 x 50.0 x 8.00 mm

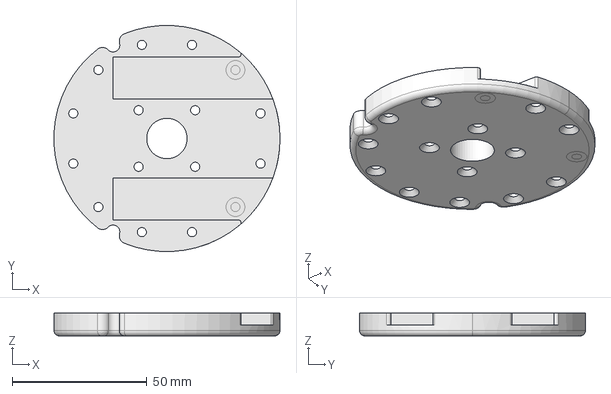
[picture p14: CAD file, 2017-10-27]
CAD/Leg/UpperKnee3B-15_5mm.FCStd
83.9 x 83.9 x 8.50 mm

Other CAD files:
CAD/TestRigs/GearBoxDrawing.fcstd
CAD/Servo/MotorMountPD5060v3.FCStd
CAD/TestRigs/TestRig_bearing-seat.fcstd
CAD/Body/MotorDriverMount.FCStd
CAD/Body/BatteryMount.FCStd
CAD/Body/BatteryMountV2.FCStd
CAD/Body/BodyBracketA.FCStd
CAD/Body/CableClamp.FCStd
CAD/Body/DriveMountStandoff.FCStd
CAD/Body/LegSpacer.fcstd
CAD/Body/Plate_001.fcstd
CAD/Body/PoweBarLid.FCStd
CAD/Body/PowerBar.FCStd
CAD/Body/Spacer.FCStd
CAD/Leg/DriveLink.FCStd
CAD/Leg/DriveLinkB-15mm.FCStd
CAD/Leg/DriveLinkV2-15mm.FCStd
CAD/Leg/DriveLink_15mm.FCStd
CAD/Leg/Foot.FCStd
CAD/Leg/KneeBearingCage.FCStd
CAD/Leg/KneePushRodMount.FCStd
CAD/Leg/LegMount.FCStd
CAD/Leg/LegMountV2-15_5mm.FCStd
CAD/Leg/LegMountV2-15mm.FCStd
CAD/Leg/LegMountV2.FCStd
CAD/Leg/LegMovementSim.FCStd
CAD/Leg/LegSpacer.fcstd
CAD/Leg/LowerKnee.FCStd
CAD/Leg/LowerKneeRace.FCStd
CAD/Leg/LowerKneeRaceV2.FCStd
CAD/Leg/LowerKneeRaceV3.FCStd
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

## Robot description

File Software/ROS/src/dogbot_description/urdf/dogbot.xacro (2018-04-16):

<?xml version="1.0"?>
<robot name="dogbot" xmlns:xacro="http://ros.org/wiki/xacro">

  <xacro:property name="bodyheight" value="0.1" />
  <xacro:property name="bodywidth" value="0.38" />
  <xacro:property name="bodylen" value="0.43" />
  <xacro:property name="legoffset" value="0.125" />

  <xacro:property name="drivediam" value="0.08" />
  
  <xacro:property name="upperleglen" value="0.36" />
  <xacro:property name="lowerleglen" value="0.31" />
  
  <xacro:property name="pi" value="3.1415" />

  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

  <xacro:macro name="default_inertial" params="mass">
    <inertial>
      <mass value="${mass}" />
      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
    </inertial>
  </xacro:macro>

  <link name="base_link">
  </link>

  <link name="body">
    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
        
    <xacro:default_inertial mass="4"/>

        
  </link>

  <joint name="base_joint" type="fixed">
    <axis xyz="0 0 0" rpy="0 0 0" />
    <parent link="base_link"/>
    <child link="body"/>
  </joint>

  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
   
  <xacro:macro name="leg" params="prefix suffix reflectx reflecty">
    <link name="${prefix}_${suffix}_hip">
      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
      <xacro:default_inertial mass="1"/>
    </link>    
    
    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
    
    <joint name="${prefix}_${suffix}_roll_joint" type="revolute">
      <axis xyz="0 1 0" rpy="0 0 0" />
      <parent link="body"/>
      <child link="${prefix}_${suffix}_hip"/>
      <origin xyz="${legoffset*reflectx} ${bodylen * reflecty/2} 0" rpy="0 0 ${-pi*(1-reflecty)/2}"/>
      <limit lower ="${(-pi * (reflectx * reflecty +1)/2) + (pi * (reflectx * reflecty -1)/8) }" upper ="${(-pi * (reflectx * reflecty -1)/2) + (pi * (reflectx * reflecty +1)/8) }" effort="500" velocity="10.0" />
    </joint>

    <link name="${prefix}_${suffix}_upperleg">
      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
      <xacro:default_inertial mass="0.7"/>
    </link>    

    <joint name="${prefix}_${suffix}_pitch_joint" type="revolute">
      <axis xyz="0 1 0" rpy="0 0 0" />
      <parent link="${prefix}_${suffix}_hip"/>
      <child link="${prefix}_${suffix}_upperleg"/>
      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
      <origin xyz="${0.04*reflectx*reflecty} 0.07 -0.080" rpy="0 ${pi * reflectx/2} ${pi *reflectx *reflecty /2}"/>
      <limit lower ="-${pi/2}" upper="${pi/2}" effort="500" velocity="10.0" />
    </joint>

    <link name="${prefix}_${suffix}_lowerleg">
      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
      <xacro:default_inertial mass="0.3"/>
    </link>    

    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
    
    <joint name="${prefix}_${suffix}_knee_joint" type="revolute">
      <axis xyz="0 1 0" rpy="0 0 0" />
      <parent link="${prefix}_${suffix}_upperleg"/>
      <child link="${prefix}_${suffix}_lowerleg"/>
      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
      <origin xyz="${upperleglen * reflectx} 0 0" rpy="0 0 0"/>
      <limit lower ="${(pi * reflectx - pi) }" upper ="${(pi * reflectx + pi) }" effort="500" velocity="10.0" />
    </joint>

    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
    
  </xacro:macro>

  <xacro:leg prefix="front" suffix="right" reflectx="-1" reflecty="-1"/>
  <xacro:leg prefix="front" suffix="left" reflectx="1" reflecty="-1" />
  <xacro:leg prefix="back" suffix="right" reflectx="-1" reflecty="1"/>
  <xacro:leg prefix="back" suffix="left" reflectx="1" reflecty="1" />

  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


</robot>

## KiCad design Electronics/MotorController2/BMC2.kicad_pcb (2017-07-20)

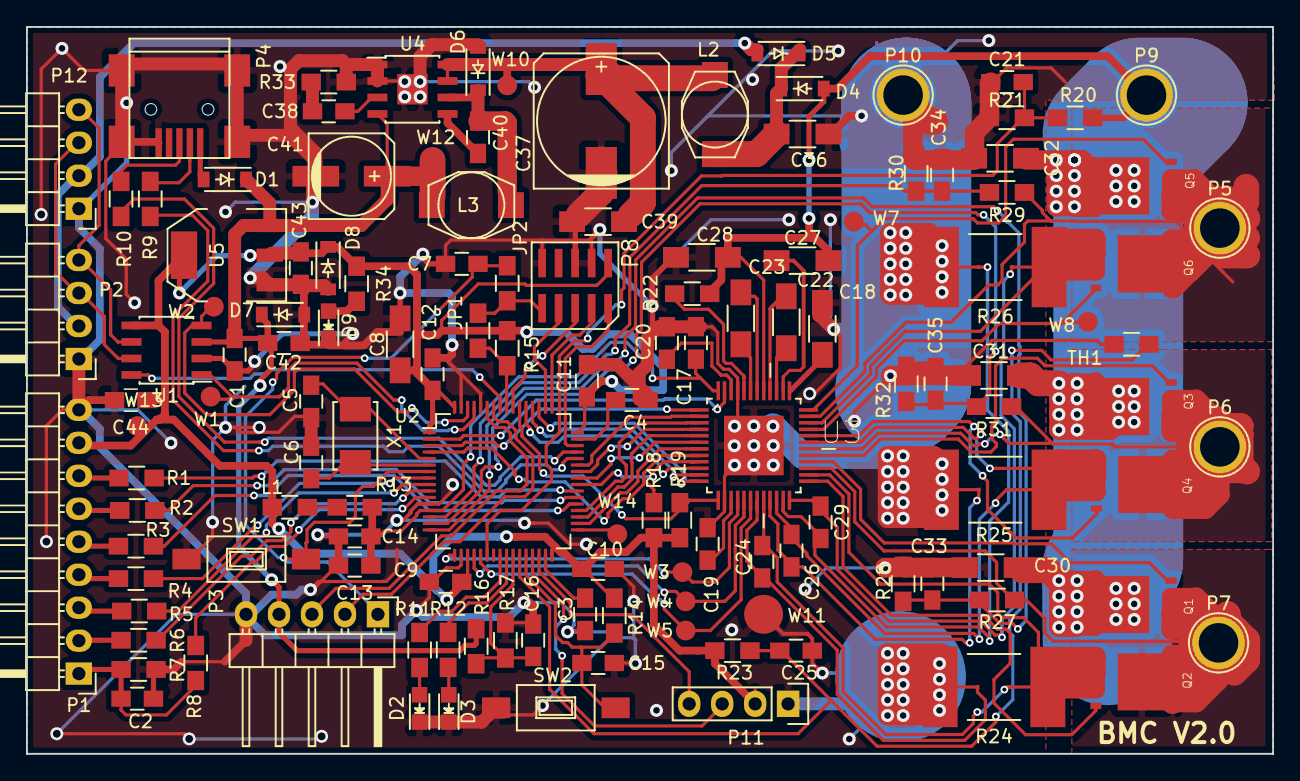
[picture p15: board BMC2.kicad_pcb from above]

Board: 2 copper layers, 96.0 x 56.0 mm, 131 parts (0 on the bottom side), 109 nets.

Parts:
C1, C44: 0.1uf (6V min); C_0805_HandSoldering
C2: 0.1uF; C_0805_HandSoldering
C3, C4: 2.2uf; C_0805_HandSoldering
C5, C6: 15pF; C_0805_HandSoldering
C7, C10, C11, C12: 100nf; C_0805_HandSoldering
C8: 4.7uf; C_1206_HandSoldering
C9: 100nf 5V; C_0805_HandSoldering
C13: 10nf; C_0805_HandSoldering
C14: 1uf; C_0805_HandSoldering
C15, C16, C21, C25: 0.1uF 5V; C_0805_HandSoldering
C17: 1uF 4V; C_0805_HandSoldering
C18: 1uf 16V; C_1206_HandSoldering
C19, C20: 1uf 6.3V; C_0805_HandSoldering
C22: 0.047uf 90V; C_1206_HandSoldering
C23: 0.047uf 45v; C_1206_HandSoldering
C24, C26: 1nF 5V; C_0805_HandSoldering
C27: 2.2uf 16V; C_1206_HandSoldering
C28: 4.7uF 45V; C_1206_HandSoldering
C29: 1nf 5V; C_0805_HandSoldering
C30, C31, C32: 1uF 50V; C_1206_HandSoldering
C33, C34, C35: 30pF 5V; C_0805_HandSoldering
C36, C39: 220nF 60V; C_1206_HandSoldering
C37: 100uF 60V; c_elec_10x10.5
C38: 22nF 6V; C_0805_HandSoldering
C40, C42: 220nF 6V; C_0805_HandSoldering
C41: 100uF 6V; c_elec_6.3x5.8
C43: 1uF 4V min; C_0805_HandSoldering
D1: 10V; SOD-123
D2: GREEN LED; LED_0805
D3: RED LED; LED_0805
D4, D5: 60V 2A; SOD-123
D6: 50V; SOD-123
D7: 5.4V; SOD-123
D8: 3.6V; SOD-123
D9: LED; LED_0805
JP1: Jumper_NO_Small; R_0805_HandSoldering
JP2: Jumper_NC_Small; R_0805_HandSoldering
L1: 10uH; R_0805_HandSoldering
L2, L3: 47uH; SELF-WE-PD3S
P1: Sensor; Pin_Header_Angled_1x09
P2, P12: CAN; Pin_Header_Angled_1x04
P3: DATA; Pin_Header_Angled_1x05
P4: USB_OTG; USB_Mini-B
P5: PhaseA; 1pin
P6: PhaseB; 1pin
P7: PhaseC; 1pin
P8: CONN_02X05; SMT-HDR-10
P9: VSUPPLY; 1pin
P10: GND; 1pin
P11: I2C; Pin_Header_Straight_1x04
Q1, Q2, Q3, Q4, Q5, Q6: BSC016N06NS; SON127P532X615X110-8N
R1, R2, R3, R4, R5, R6, R8: 1k; R_0805_HandSoldering
R7: 10k; R_0805_HandSoldering
R9, R10: 22R; R_0805_HandSoldering
R11, R12, R22, R34: 100R; R_0805_HandSoldering
R13: 10; R_0805_HandSoldering
R14, R15, R16, R17, R18, R19, R23: 10K; R_0805_HandSoldering
R20, R27, R29, R31: 39K; R_0805_HandSoldering
R21, R28, R30, R32: 3K; R_0805_HandSoldering
R24, R25, R26: R001; R_PSR400_SENSE
R33: 22k; R_0805_HandSoldering
SW1: RESET; SW_SPST_FSMSM
SW2: CAL; SW_SPST_FSMSM
TH1: THERMISTOR; R_0805_HandSoldering
U1: TJA1042T/3; SOIC-8_3.9x4.9mm_Pitch1.27mm
U2: STM32F205RBTx; LQFP-64_10x10mm_Pitch0.5mm
U3: DRV8305; QFP50P900X900X120-49N
U4: IFX91041EJV50; SOIC-8-1EP_3.9x4.9mm_Pitch1.27mm
U5: TC2117-3.3V; SOT-223
W1: CAN_TX; Measurement_Point_Round-SMD-Pad_Small
W2: CAN_RX; Measurement_Point_Round-SMD-Pad_Small
W3: ISenseA; Measurement_Point_Round-SMD-Pad_Small
W4: ISenseB; Measurement_Point_Round-SMD-Pad_Small
W5: ISenseC; Measurement_Point_Round-SMD-Pad_Small
W7: GHA; Measurement_Point_Round-SMD-Pad_Small
W8: GLA; Measurement_Point_Round-SMD-Pad_Small
W10: DSUP; Measurement_Point_Round-SMD-Pad_Small
W11: GND; Measurement_Point_Round-SMD-Pad_Big
W12: 5V; Measurement_Point_Round-SMD-Pad_Small
W13: 3V3; Measurement_Point_Round-SMD-Pad_Small
W14: PB12; Measurement_Point_Round-SMD-Pad_Small
X1: 8MHz; ABM3

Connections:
+3.3VADC: C13.1, C14.1, C17.1, R13.1, U2.13, U3.48
+3V3: C8.1, C9.1, C10.1, C11.1, C12.1, C43.1, C44.1, D8.1, L1.1, P1.8, P8.1, P11.2, R14.1, R15.2, R18.1, R19.1, R23.1, R34.1, U1.5, U2.1, U2.19, U2.32, U2.48, U2.64, U5.2, U5.4, W13.1
+5V: C1.1, C41.1, C42.1, D1.1, D7.1, L3.1, P3.4, R16.1, U1.3, U4.4, U5.3, W12.1
+8V: D5.2, P2.2, P12.2
+36V: C27.2, C28.1, C30.1, C31.1, C32.1, D4.2, P9.1, Q1.5, Q1.6, Q1.7, Q1.8, Q3.5, Q3.6, Q3.7, Q3.8, Q5.5, Q5.6, Q5.7, Q5.8, R20.1, R22.1, U3.41
/Controller/CAN_RX: U1.4, U2.62, W2.1
/Controller/CAN_STBY: U1.8, U2.57
/Controller/CAN_TX: U1.1, U2.61, W1.1
/Controller/EN_GATE: U2.3, U3.1
/Controller/EndStop1: R3.1, U2.37
/Controller/EndStop2: R2.1, U2.38
/Controller/FAULT: R18.2, U2.4, U3.8
/Controller/HallA: R4.1, U2.8
/Controller/HallB: R5.1, U2.9
/Controller/HallC: R6.1, U2.10
/Controller/I2C_SCL: P11.3, U2.29
/Controller/I2C_SDA: P11.4, U2.30
/Controller/INHA: U2.43, U3.2
/Controller/INHB: U2.42, U3.4
/Controller/INHC: U2.41, U3.6
/Controller/INLA: U2.36, U3.3
/Controller/INLB: U2.35, U3.5
/Controller/INLC: U2.34, U3.7
/Controller/ISenseA: U2.17, U3.16, W3.1
/Controller/ISenseB: U2.20, U3.17, W4.1
/Controller/ISenseC: U2.21, U3.18, W5.1
/Controller/Index: R1.1, U2.39
/Controller/MISO: U2.52, U3.11
/Controller/MOSI: U2.53, U3.10
/Controller/PWRGD: R19.2, U2.54, U3.13
/Controller/SCLK: U2.51, U3.12
/Controller/Temp: R8.1, U2.11
/Controller/TempDrv: C25.1, R23.2, TH1.1, U2.27
/Controller/UART_RX: P3.3, U2.59
/Controller/UART_TX: P3.2, U2.58
/Controller/USB_DM: R9.1, U2.44
/Controller/USB_DP: R10.1, U2.45
/Controller/VSenseA: C34.1, R29.2, R30.1, U2.14
/Controller/VSenseB: C35.1, R31.2, R32.1, U2.15
/Controller/VSenseC: C33.1, R27.2, R28.1, U2.16
/Controller/VSenseSupply: C21.1, R20.2, R21.1, U2.22
/Controller/sSCS: U2.40, U3.9
/power/PhaseA: P5.1, Q5.1, Q5.2, Q5.3, Q6.5, Q6.6, Q6.7, Q6.8, R29.1, U3.35
/power/PhaseB: P6.1, Q3.1, Q3.2, Q3.3, Q4.5, Q4.6, Q4.7, Q4.8, R31.1, U3.30
/power/PhaseC: P7.1, Q1.1, Q1.2, Q1.3, Q2.5, Q2.6, Q2.7, Q2.8, R27.1, U3.27
/power/WAKE: U2.2, U3.47
GND: C1.2, C2.2, C3.2, C4.2, C5.2, C6.2, C7.2, C8.2, C9.2, C10.2, C11.2, C12.2, C13.2, C14.2, C15.2, C16.2, C17.2, C18.2, C19.2, C20.2, C21.2, C25.2, C28.2, C30.2, C31.2, C32.2, C33.2, C34.2, C35.2, C36.2, C37.2, C39.2, C41.2, C42.2, C43.2, C44.2, D2.1, D3.1, D6.2, D7.2, D8.2, D9.1, P1.9, P2.1, P3.5, P4.5, P4.6, P8.3, P8.5, P8.9, P10.1, P11.1, P12.1, R7.2, R17.2, R21.2, R24.4, R25.4, R26.4, R28.2, R30.2, R32.2, R33.2, SW1.1, SW2.2, TH1.2, U1.2, U2.12, U2.18, U2.60, U2.63, U3.14, U3.45, U3.49, U4.1, U4.2, U4.9, U5.1, W11.1
NRST: C7.1, JP2.2, P3.1, SW1.2, U2.7
unnamed: C2.1, P1.1, R7.1, R8.2
unnamed: C3.1, U2.31
unnamed: C4.1, U2.47
unnamed: C5.1, U2.5, X1.1
unnamed: C6.1, U2.6, X1.2
unnamed: C15.1, R14.2, SW2.1, U2.28
unnamed: C16.1, R16.2, R17.1, U2.26
unnamed: C18.1, U3.37
unnamed: C19.1, U3.15
unnamed: C20.1, U3.46
unnamed: C22.1, U3.39
unnamed: C22.2, U3.40
unnamed: C23.1, U3.43
unnamed: C23.2, U3.42
unnamed: C24.1, R24.2, U3.20
unnamed: C24.2, R24.3, U3.19
unnamed: C26.1, R25.2, U3.22
unnamed: C26.2, R25.3, U3.21
unnamed: C27.1, U3.38
unnamed: C29.1, R26.2, U3.24
unnamed: C29.2, R26.3, U3.23
unnamed: C36.1, D4.1, D5.1, L2.2
unnamed: C37.1, C39.1, L2.1, U4.7, U4.8, W10.1
unnamed: C38.1, U4.3
unnamed: C38.2, R33.1
unnamed: C40.1, U4.5
unnamed: C40.2, D6.1, L3.2, U4.6
unnamed: D1.2, P4.1
unnamed: D2.2, R11.2
unnamed: D3.2, R12.2
unnamed: D9.2, R34.2
unnamed: JP1.1, R15.1, U2.56
unnamed: JP1.2, JP2.1, P8.10
unnamed: L1.2, R13.2
unnamed: P1.2, R6.2
unnamed: P1.3, R5.2
unnamed: P1.4, R4.2
unnamed: P1.5, R3.2
unnamed: P1.6, R2.2
unnamed: P1.7, R1.2
unnamed: P4.2, R9.2
unnamed: P4.3, R10.2
unnamed: P8.2, U2.46
unnamed: P8.4, U2.49
unnamed: P8.6, U2.55
unnamed: P8.8, U2.50
unnamed: P2.3, P12.3, U1.7
unnamed: P2.4, P12.4, U1.6
unnamed: Q1.4, U3.28
unnamed: Q2.1, Q2.2, Q2.3, R24.1, U3.26
unnamed: Q2.4, U3.25
unnamed: Q3.4, U3.29
unnamed: Q4.1, Q4.2, Q4.3, R25.1, U3.31
unnamed: Q4.4, U3.32
unnamed: Q5.4, U3.36, W7.1
unnamed: Q6.1, Q6.2, Q6.3, R26.1, U3.34
unnamed: Q6.4, U3.33, W8.1
unnamed: R11.1, U2.24
unnamed: R12.1, U2.25
unnamed: R22.2, U3.44
unnamed: U2.33, W14.1

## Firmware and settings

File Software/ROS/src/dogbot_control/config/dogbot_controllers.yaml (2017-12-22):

# ros_control_boilerplate Settings -----------------------
# Settings for ros_control control loop
dogbot_hw_control_loop:
  loop_hz: 100
  cycle_time_error_threshold: 0.03

# Settings for ros_control hardware interface
hardware_interface:
   joints:
      - front_right_roll_joint
      - front_right_pitch_joint
      - front_right_knee_joint
      - front_left_roll_joint
      - front_left_pitch_joint
      - front_left_knee_joint
      - back_right_roll_joint
      - back_right_pitch_joint
      - back_right_knee_joint
      - back_left_roll_joint
      - back_left_pitch_joint
      - back_left_knee_joint
   sim_control_mode: 1 # 0: position, 1: velocity

# Publish all joint states ----------------------------------
# Creates the /joint_states topic necessary in ROS
joint_state_controller:
   type:         joint_state_controller/JointStateController
   publish_rate: 50


# Individual Position Controllers ---------------------------------------
# Allows to send individual ROS msg of Float64 to each joint separately
front_right_roll_position_controller:
   type: position_controllers/JointPositionController
   joint: front_right_roll_joint
   pid: {p: 100.0, i: 0.01, d: 10.0}
front_right_pitch_position_controller:
   type: position_controllers/JointPositionController
   joint: front_right_pitch_joint
   pid: {p: 100.0, i: 0.01, d: 10.0}
front_right_knee_position_controller:
   type: position_controllers/JointPositionController
   joint: front_right_knee_joint
   pid: {p: 100.0, i: 0.01, d: 10.0}
   
front_left_roll_position_controller:
   type: position_controllers/JointPositionController
   joint: front_left_roll_joint
   pid: {p: 100.0, i: 0.01, d: 10.0}
front_left_pitch_position_controller:
   type: position_controllers/JointPositionController
   joint: front_left_pitch_joint
   pid: {p: 100.0, i: 0.01, d: 10.0}
front_left_knee_position_controller:
   type: position_controllers/JointPositionController
   joint: front_left_knee_joint
   pid: {p: 100.0, i: 0.01, d: 10.0}

back_right_roll_position_controller:
   type: position_controllers/JointPositionController
   joint: back_right_roll_joint
   pid: {p: 100.0, i: 0.01, d: 10.0}
back_right_pitch_position_controller:
   type: position_controllers/JointPositionController
   joint: back_right_pitch_joint
   pid: {p: 100.0, i: 0.01, d: 10.0}
back_right_knee_position_controller:
   type: position_controllers/JointPositionController
   joint: back_right_knee_joint
   pid: {p: 100.0, i: 0.01, d: 10.0}
   
back_left_roll_position_controller:
   type: position_controllers/JointPositionController
   joint: back_left_roll_joint
   pid: {p: 100.0, i: 0.01, d: 10.0}
back_left_pitch_position_controller:
   type: position_controllers/JointPositionController
   joint: back_left_pitch_joint
   pid: {p: 100.0, i: 0.01, d: 10.0}
back_left_knee_position_controller:
   type: position_controllers/JointPositionController
   joint: back_left_knee_joint
   pid: {p: 100.0, i: 0.01, d: 10.0}

# Group Position Controllers ---------------------------------------
# Allows to send single ROS msg of Float64MultiArray to all joints
joint_position_controller:
   type: position_controllers/JointGroupPositionController
   joints:
      - front_right_roll_joint
      - front_right_pitch_joint
      - front_right_knee_joint
      - front_left_roll_joint
      - front_left_pitch_joint
      - front_left_knee_joint
      - back_right_roll_joint
      - back_right_pitch_joint
      - back_right_knee_joint
      - back_left_roll_joint
      - back_left_pitch_joint
      - back_left_knee_joint
     
# Joint Trajectory Controller -------------------------------
# For detailed explanations of parameter see http://wiki.ros.org/joint_trajectory_controller
position_trajectory_controller:
   type: position_controllers/JointTrajectoryController
   # These joints can likely just be copied from the hardware_interface list above
   joints:
      - front_right_roll_joint
      - front_right_pitch_joint
      - front_right_knee_joint
      - front_left_roll_joint
      - front_left_pitch_joint
      - front_left_knee_joint
      - back_right_roll_joint
      - back_right_pitch_joint
      - back_right_knee_joint
      - back_left_roll_joint
      - back_left_pitch_joint
      - back_left_knee_joint
   constraints:
      goal_time: 5.0
      #stopped_position_tolerance: 0.4 # Defaults to 0.01
      front_right_roll_joint:
          trajectory: 0.60
          goal:       0.15
      front_right_pitch_joint:
          trajectory: 0.60
          goal:       0.15
   # gains:
   #     joint1: {p: 2.0,  i: 0.0, d: 0.01, i_clamp: 1}
   #     joint2: {p: 2.0,  i: 0.0, d: 0.01, i_clamp: 1}

    # state_publish_rate:  50 # Defaults to 50
    # action_monitor_rate: 20 # Defaults to 20
    #hold_trajectory_duration: 0 # Defaults to 0.5
     

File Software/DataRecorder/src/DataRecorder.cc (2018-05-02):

#include "dogbot/DataRecorder.hh"
#include <math.h>

namespace DogBotN {

  PGDataRecorderC::PGLogEntryC::PGLogEntryC(bool isCommand,const uint8_t *data,int len)
   : m_isCommand(isCommand),
     m_len(len)
  {
    gettimeofday(&m_when,0);
    if(len > sizeof(m_data))
      len = sizeof(m_data);
    memcpy(m_data,data,len);
  }

  // -----------------------------------------------------------------------------

  PGDataRecorderC::PGDataRecorderC(const std::shared_ptr<DogBotAPIC> &api,const std::string &databaseConnectionStr)
    : m_api(api),
      m_coms(api->Connection()),
      m_databaseConnectionString(databaseConnectionStr),
      m_connection(databaseConnectionStr)
  {
    m_recordQueue.reserve(256);
    m_recordQueueWrite.reserve(256);
  }

  //! Destructor, this will wait for the write thread to complete
  //! its current write and exit.
  PGDataRecorderC::~PGDataRecorderC()
  {
    m_terminated = true;
    if(m_writeThread.joinable())
      m_writeThread.join();
  }

  //! Create schema in database.
  void PGDataRecorderC::CreateSchema()
  {
    //pqxx::connection dbcon(m_databaseConnectionString);
    //pqxx::work txn(m_connection,"Create schema");


  }

  //! Find the name for a device
  std::string PGDataRecorderC::DeviceName(int deviceId)
  {
    assert(deviceId < 256);
    if(deviceId < 0 || deviceId > 255)
      return "Invalid";
    std::lock_guard<std::mutex> lock(m_accessDeviceData);

    while(deviceId >= m_deviceNames.size()) {
      m_deviceNames.push_back(std::string());
    }
    if(m_deviceNames[deviceId].empty()) {
      auto servoPtr = m_api->GetServoById(deviceId);
      if(!servoPtr)
        return std::to_string(deviceId);
      m_deviceNames[deviceId] = servoPtr->Name();
    }
    return m_deviceNames[deviceId];
  }


  static std::string AsISO8601(const struct timeval &when) {
    struct tm b;

    //static double offset = (double) (std::chrono::system_clock::now() - StdTimeT::clock::now()).count();

    double seconds =0;
    double fract = (double) when.tv_usec / 1000000.0;

    time_t s =  when.tv_sec;

    gmtime_r(&s,&b);
    const int buffSize = 64;
    std::string ret(buffSize,0);

    //std::cerr << "Seconds:" << seconds << " Fract:" << fract << " Year:" << b.tm_year << " "  << std::endl;

    double sec = (double) b.tm_sec + fract;
    int len = 0;
    if(b.tm_sec < 10) {
      len = snprintf(&ret[0],buffSize,"%04u-%02u-%02uT%02u:%02u:0%1fZ",b.tm_year + 1900,b.tm_mon+1,b.tm_mday,b.tm_hour,b.tm_min,sec);
    } else {
      len = snprintf(&ret[0],buffSize,"%04u-%02u-%02uT%02u:%02u:%2fZ",b.tm_year + 1900,b.tm_mon+1,b.tm_mday,b.tm_hour,b.tm_min,sec);
    }
    ret.resize(len);
    //std::cerr << "Time : " << ret << std::endl;
    return ret;
  }

  //! Log a servo report message.
  bool PGDataRecorderC::LogServoReport(pqxx::work &txn,std::string &query,PGLogEntryC &a)
  {
    if(a.m_len != sizeof(struct PacketServoReportC)) {
      m_log->error("Unexpected 'ServoReport' packet length {} ",a.m_len);
      return false;
    }
    const PacketServoReportC *pkt = (const PacketServoReportC *) a.m_data;

    if(query.empty()) {
      query.reserve(4096);
      query += "INSERT INTO joint_report (sourceid,logtime,synctime,position,velocity,effort,reference,position_limit,torque_limit,velocity_limit,index_sensor) VALUES ";
    } else
      query += ",";

    query += "(";
    query += txn.quote(DeviceName(pkt->m_deviceId));
    query += ",";
    query += txn.quote(AsISO8601(a.m_when));
    query += ",";
    query += txn.quote((unsigned) pkt->m_timestamp);
    query += ",";
    query += txn.quote(ComsC::PositionReport2Angle(pkt->m_position));
    query += ",";
    query += txn.quote(ComsC::VelocityReport2Angle(pkt->m_velocity));
    query += ",";
    query += txn.quote(ComsC::TorqueReport2Fraction(pkt->m_torque));
    query += ",";
    query += txn.quote(ComsPositionRefrenceToString((enum PositionReferenceT)(pkt->m_mode & DOGBOT_SERVOREPORTMODE_POSITIONREF)));
    query += ",";
    query += txn.quote((pkt->m_mode & DOGBOT_SERVOREPORTMODE_LIMITPOSITION) != 0);
    query += ",";
    query += txn.quote((pkt->m_mode & DOGBOT_SERVOREPORTMODE_LIMITTORQUE) != 0);
    query += ",";
    query += txn.quote((pkt->m_mode & DOGBOT_SERVOREPORTMODE_LIMITVELOCITY) != 0);
    query += ",";
    query += txn.quote((pkt->m_mode & DOGBOT_SERVOREPORTMODE_INDEXSENSOR) != 0);
    query += ")";

    return true;
  }


  //! Log a servo demand message.
  bool PGDataRecorderC::LogServo(pqxx::work &txn,std::string &query,PGLogEntryC &a)
  {
    if(a.m_len != sizeof(struct PacketServoC)) {
      m_log->error("Unexpected 'Servo' packet length {} ",a.m_len);
      return false;
    }
    const PacketServoC *pkt = (const PacketServoC *) a.m_data;
    if(query.empty()) {
      query.reserve(4096);
      query += "INSERT INTO joint_demand (sourceid,logtime,position,effort_limit) VALUES ";
    } else
      query += ",";

    query += "(";
    query += txn.quote(DeviceName(pkt->m_deviceId));
    query += ",";
    query += txn.quote(AsISO8601(a.m_when));
    query += ",";
    query += txn.quote(ComsC::PositionReport2Angle(pkt->m_position));
    query += ",";
    query += txn.quote((double) pkt->m_torqueLimit / 65535.0);
    query += ")";

    return true;
  }

  //! Log a parameter report message
  bool PGDataRecorderC::LogParamReport(pqxx::work &txn,std::string &query,PGLogEntryC &a)
  {
    const PacketParam8ByteC *pkt = (const PacketParam8ByteC *) a.m_data;

    if(query.empty()) {
      query.reserve(4096);
      query += "INSERT INTO parameter_report (sourceid,logtime,parameter,value) VALUES ";
    } else
      query += ",";
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

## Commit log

2017-07-20 Added current CAD and motor controller schematics.
    [BMC2.csv, BMC2.kicad_pcb, BMC2.sch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]
2017-07-20 Add pointer to motor controller firmware.
2017-07-21 Add dogbot urdf file.
    [dogbot.xacro]
2017-08-10 created Plate_001 in FreeCAD
    [Plate_001.fcstd]
2017-08-11 Added CAD for new split delvis design
2017-08-13 Add access holes.
2017-08-17 Add place to put cable tie.
    [MotorHall3SensorMount.FCStd]
2017-08-17 Add standoff for motor driver mounts.
    [DriveMountStandoff.FCStd]
2017-08-27 Updates and new parts.
    [BatteryMount.FCStd, CableClamp.FCStd, EndStopSensorMount.FCStd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]
2017-08-29 Add capacitor connection cover, and increase number of positions for end stop sensors.
    [CableClamp.FCStd, CapacitorConnectionCover.FCStd, EndStopSensorMount.FCStd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]
2017-08-31 Add add lenght pad for rods.
    [Pad.fcstd]
2017-08-31 Move thermocouple hole so the screw hole is accessible for fixing, add leg spacer, fix battery mount.
    [BatteryMount.FCStd, LegSpacer.fcstd, MotorMountMT5208.FCStd]
2017-09-04 Add place for temprature sensor in motor mount. Make sure there is a cable clamp for data wires.
    [CableClamp.FCStd, DriveMountStandoff.FCStd, LegSpacer.fcstd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]
2017-09-04 Move boards to give more clearence for the connectors on the body mounted controllers.
    [MotorDriverMount.FCStd, MotorDriverMountB.FCStd]
2017-09-05 Add missing chamfer.
    [UpperKnee3B.FCStd]
2017-09-10 Add temprature sensor cover, fix motor drive mount cover.
    [LegSpacer.fcstd, MotorDriverMount.FCStd, MotorDriverMountB.FCStd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]
2017-09-11 Add other side of battery mount.
    [BatteryMount.FCStd]
2017-09-15 Notes on states of driver boards.
2017-09-19 Change hole spacing on pelvis.
2017-09-25 New experimental lightweight parts.
    [CarrierAV2.FCStd, DriveLink.FCStd, LowerKneeRace.FCStd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]
2017-09-26 Change carrier to 3mm, add FixedRing 1_5.
    [CarrierAV2.FCStd, PlanetGear12_18_SmallV2.FCStd]
2017-09-29 new motos cowling for large motor and bearing housings for test jig
    [MotorMountPD5060v1.fcstd, TestRig_DummyRingDrive3.fcstd, TestRig_bearing-housing.fcstd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]
2017-09-29 Allow link between servos
    [DriveLink.FCStd, LegMountV2.FCStd]
2017-09-29 Carrier renamed and increased spacing for washers.
    [CarrierAV2.FCStd, CarrierV2.FCStd]
2017-09-29 motor adapter for propdrive motor
    [MotorAdaptorV2wide.FCStd]
2017-10-01 Work on new gearbox.
    [CarrierAV2_old.FCStd, CarrierV2.FCStd, DriveLink.FCStd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]
2017-10-02 Misc fixes.
    [MotorAdaptorV2wide.FCStd, MotorMountPD5060v2.FCStd]
2017-10-03 Fix overhang problem in rod recess.
2017-10-03 Tweak dimensions.
    [MotorAdaptorV2wide.FCStd]
2017-10-06 large motor cowling - mods for hall sensor
    [MotorHall3SensorMountV3.FCStd]
2017-10-06 servo blinding + battery mount clips
    [BatteryMountV2.FCStd, CarrierV3.FCStd, PlanetGear12_18_SmallV3.FCStd]
2017-10-07 Fixes for printability.
    [CarrierV3.FCStd, MotorMountMT5208V3.FCStd, MotorMountPD5060v3.FCStd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]
2017-10-10 PD5060 sensor mount, and PCB version.
    [MotorHall3SensorMountPCB.FCStd, MotorHall3SensorMountPD5060.FCStd]
2017-10-13 changes for 15mm CF rods - some still to do, see notes
    [DriveLink_15mm.FCStd, GearBoxDrawing.fcstd, LegMountV2-15mm.FCStd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]
2017-10-17 Make parts the same size.
    [PushRodTailB_short.FCStd]
2017-10-18 Fix short tails, add wide-long motor adaptor.
    [MotorAdaptorV2wide_long.FCStd, PushRodTailB_short.FCStd, PushRodTail_Short.FCStd]
2017-10-18 Add version of knee with end stops.
    [LowerKneeRaceV4.FCStd, MotorAdaptorV2wide_long.FCStd, UpperKnee4-15mm.FCStd]
2017-10-24 2D drawing to test gearbox spacing
    [GearBoxDrawing.fcstd]
2017-10-25 Knee updates, and add altenate drive link design.
    [DriveLinkB-15mm.FCStd, DriveLinkV2-15mm.FCStd, DriveLinkV2B-15mm.FCStd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]
2017-10-27 updates for 15.5mm rod recess
    [LegMountV2-15_5mm.FCStd, UpperKnee3B-15_5mm.FCStd, UpperKnee4-15_5mm.FCStd]
2017-10-30 Minor tweeks.
    [DriveLinkV2B-15mm.FCStd, LowerKneeRaceV4.FCStd, MotorHall3SensorMountPCB.FCStd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]
2017-11-03 new battery + breaker mount
    [BatteryMountV3.FCStd]
2017-11-09 1.5 module planets
    [PlanetGear12_18l_Large_V3.FCStd]
2017-11-20 1.45module sun gear
    [SunGearV2_145mod.FCStd]
2017-12-05 Work in progress for the driver node.
    [dogbot.xacro]
2017-12-08 More work on ros control.
    [dogbot.xacro, dogbot_controllers.yaml]
2017-12-22 Update interface code to synchronise timings.
    [dogbot_controllers.yaml]
2018-01-10 Updates for changes to driver code.
2018-01-31 readme updates and test-rig config files
    [testrig_controllers.yaml]
2018-03-29 refactor of packages
    [dogbot.xacro]
2018-04-08 added joint movement demo to gazebo
2018-04-12 Log joint velocity estimates.
2018-04-13 Add more information about the joint.
